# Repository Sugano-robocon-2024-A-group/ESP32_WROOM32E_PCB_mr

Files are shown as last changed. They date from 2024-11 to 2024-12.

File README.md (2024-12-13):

# ESP32_WROOM_32E_msd
## 作成・許諾 
Copyright (c) [2024] [益田隆太郎]. All rights reserved.
Sugano Robocon Aチーム (益田隆太郎、大谷卓輝、須崎一眞、藤上晃成)  
### * このソフトウェアパッケージは、3条項BSDライセンスの下、再配布及び使用が許可されます
### @ 2024 Sugano Robocon A team
連絡はX(@Masuda_moto)またはryutaro.masuda@akane.waseda.jpまで
## 外観
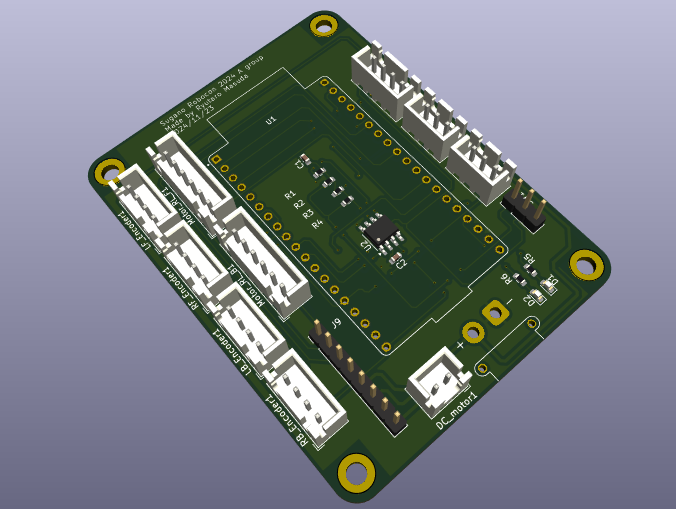
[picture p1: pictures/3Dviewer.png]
3Dviewr

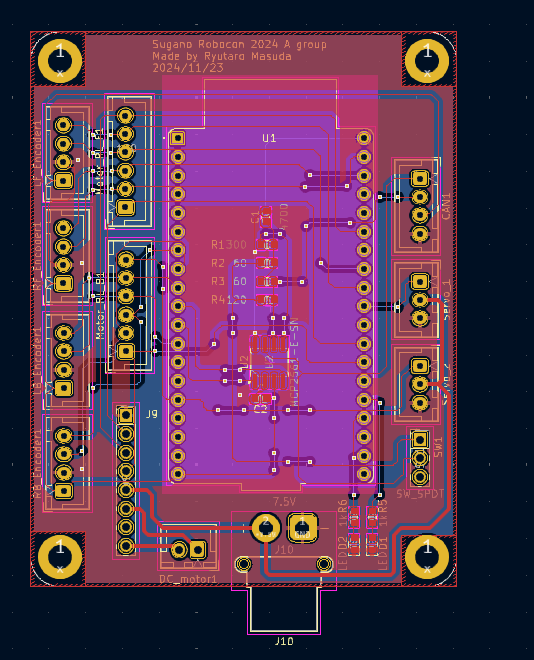
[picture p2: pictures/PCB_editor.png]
PCBViwer

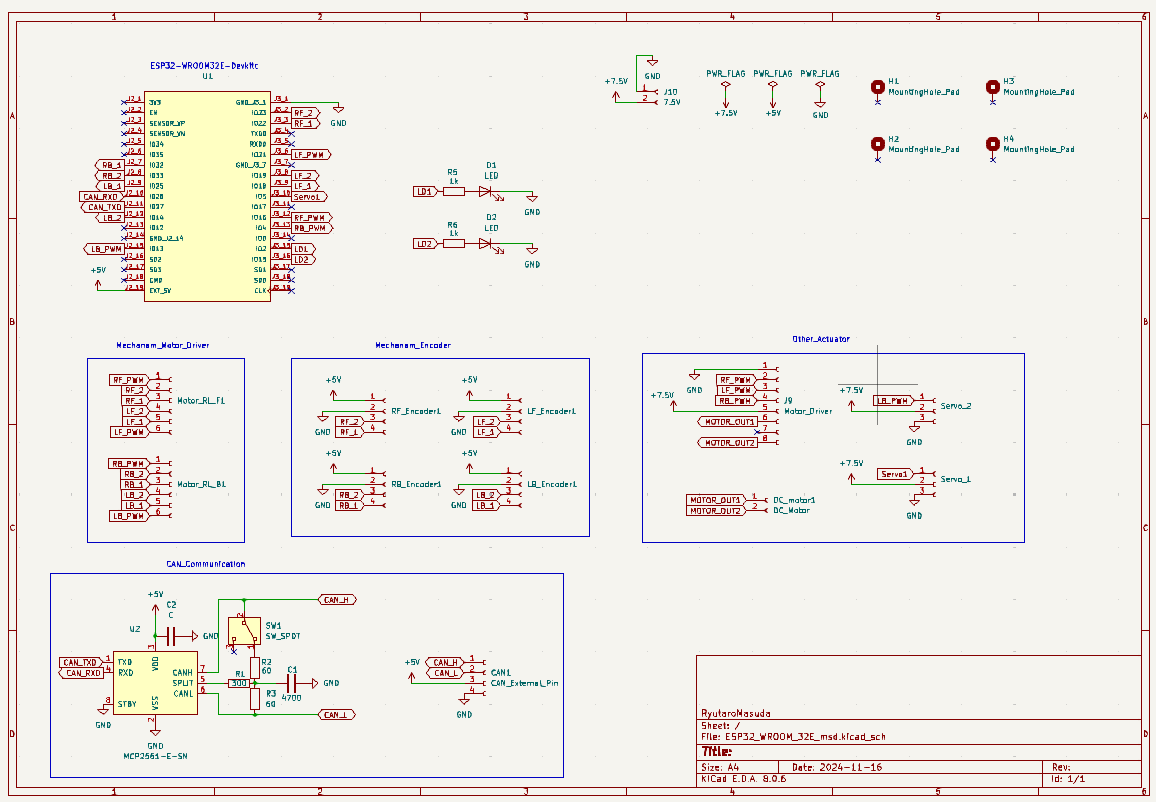
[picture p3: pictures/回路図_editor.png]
回路図

## 使用法
production→ESP32_WROOM_32E_msd.zipがガーバーファイルで、JLCPCBに送るとそのままPCBとして出してくれます。
## ピン配置
ESP32はESPマトリックス機能があるため、どのピンを使っても基本的に許されるが、PWMがはけるピンは決まっている。
[こちら](https://docs.sunfounder.com/projects/umsk/ja/latest/07_appendix/esp32_wroom_32e.html)を参照のこと
を参照のこと。
### 足回りピン配置
回路図の通りですが
RFはRightFront、LFはLeftFront、RBはRightBack、LBはLeftBackに対応しています。(例:RF_1とRF_2でモータドライバの正転逆転を制御、RF_PWMで角速度を制御)

GPIO22 RF_1  
GPIO23 RF_2  
GPIO16 RF_PWM  
GPIO18 LF_1  
GPIO19 LF_2  
GPIO21 LF_PWM  
GPIO32 RB_1  
GPIO33 RB_2  
GPIO04 RB_PWM  
GPIO25 LB_1  
GPIO14 LB_2  
GPIO13 LB_PWM  
足回りのモータドライバは[こちら](https://osoyoo.com/2022/02/25/osoyoo-model-y-4-channel-motor-driver/)の市販品を使用しました。

### CAN通信
いろんなサイトで26と27がRXとTXにアサインされていたので使用。うまく動きました。

GPIO26 CAN_RX  
GPIO27 CAN_TX  

### エンコーダピン配置
エンコーダで速度制御のフィードバックをかけたかったのですが、それだとピンが足りません。なのでマイコンを2個使って、CAN通信で情報をおくりあうことにしました。二つのマイコンの基板を共通化させたかったので、ピンを共有させました。
本番では速度のPID制御はあきらめてフィードフォワード制御に変えたので、このピンは使っていません。使いたかったら使うと良いと思います。
この場合、①RFとLFのモータを制御するマイコン②RBとLBのモータを制御するマイコン③上物を制御するマイコンの３つのマイコンでCAN通信をする必要があります。この時、CANバス内のノードが３つなので、終端抵抗を一つの基板だけOFFにする必要があります。SW1はそれ用のスイッチです。
また、ピンが共通になっているので、①のマイコンにおいて

GPIO22 RF_1  
GPIO23 RF_2  
GPIO16 RF_PWM  
GPIO18 LF_1  
GPIO19 LF_2  
GPIO21 LF_PWM  

をモータドライバに接続するときは、エンコーダに接続するピンは

GPIO32 RB_1  
GPIO33 RB_2  
GPIO25 LB_1  
GPIO14 LB_2  

であるという紛らわしさに注意する必要があります。②はその逆で、

GPIO32 RB_1  
GPIO33 RB_2  
GPIO04 RB_PWM  
GPIO25 LB_1  
GPIO14 LB_2  
GPIO13 LB_PWM  

をモータドライバに接続するので、エンコーダに接続するピンは

GPIO22 RF_1  
GPIO23 RF_2  
GPIO18 LF_1  
GPIO19 LF_2  

です。回路図の通りですね。
### 上物
投擲用のモータドライバは秋月で買える[TB67H450](https://akizukidenshi.com/catalog/g/g114753/)を使いました。
投擲のモータは速度フィードバックはかけず、フィードフォワードのみです。

GPIO16 RF_PWM 正転・逆転  
GPIO21 LF_PWM 正転・逆転  
GPIO04 RB_PWM PWM調整  

です。

GPIO13 LB_PWM  
GPIO05 Servo1  

を装填・仰角調整にアサインしました。
上物の電源電圧は2Sのリポバッテリー7.4Vを使用しました。XT30がコネクタです。

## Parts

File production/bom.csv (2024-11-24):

Designator | Footprint | Quantity | Value | LCSC Part #
C1 | 0603 | 1 | 4700
C2 | 0603 | 1 | C
CAN1 | JST_XH_B4B-XH-A_1x04_P2.50mm_Vertical | 1 | CAN_External_Pin
D1, D2 | 0603 | 2 | LED
DC_MOTOR1 | JST_XH_B2B-XH-A_1x02_P2.50mm_Vertical | 1 | DC_Motor
H1, H2, H3, H4 | MountingHole_3.2mm_M3_DIN965_Pad | 4 | MountingHole_Pad
J10 | AMASS_XT30PW-F_1x02_P2.50mm_Horizontal | 1 | 7.5V
J9 | PinHeader_1x08_P2.54mm_Vertical | 1 | Motor_Driver
LB_ENCODER1 | JST_XH_B4B-XH-A_1x04_P2.50mm_Vertical | 1 | LB_Encoder
LF_ENCODER1 | JST_XH_B4B-XH-A_1x04_P2.50mm_Vertical | 1 | LF_Encoder
MOTOR_RL_B1 | JST_XH_B6B-XH-A_1x06_P2.50mm_Vertical | 1 | Motor_RL_B
MOTOR_RL_F1 | JST_XH_B6B-XH-A_1x06_P2.50mm_Vertical | 1 | Motor_RL_F
R1 | 0603 | 1 | 300
R2, R3 | 0603 | 2 | 60
R4 | 0603 | 1 | 120
R5, R6 | 0603 | 2 | 1k
RB_ENCODER1 | JST_XH_B4B-XH-A_1x04_P2.50mm_Vertical | 1 | RB_Encoder
RF_ENCODER1 | JST_XH_B4B-XH-A_1x04_P2.50mm_Vertical | 1 | RF_Encoder
SERVO_1 | JST_XH_B3B-XH-A_1x03_P2.50mm_Vertical | 1 | Servo_1
SERVO_2 | JST_XH_B3B-XH-A_1x03_P2.50mm_Vertical | 1 | Servo_2
SW1 | PinHeader_1x03_P2.54mm_Vertical | 1 | SW_SPDT
U1 | MODULE_ESP32-DEVKITC-32E | 1 | ~
U2 | SOIC-8_3.9x4.9mm_P1.27mm | 1 | MCP2561-E-SN

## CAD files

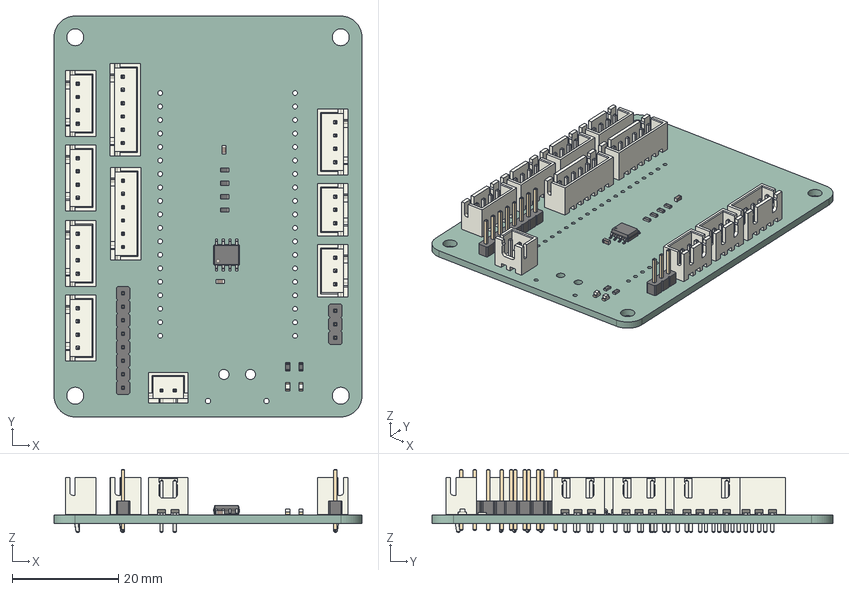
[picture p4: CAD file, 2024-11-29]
ESP32_WROOM_32E_msd.step
58.0 x 75.5 x 11.9 mm
JST_B4B_XH_A x 5
LED_0603_1608Metric x 2
C_0603_1608Metric x 2
PinHeader_1x08_P254mm_Vertical
R_0603_1608Metric x 6
SOIC_8_39x49mm_P127mm
JST_B6B_XH_A x 2
JST_B3B_XH_A x 2
JST_B2B_XH_A
PinHeader_1x03_P254mm_Vertical
_autosave-ESP32_WROOM_32E_msd_PCB

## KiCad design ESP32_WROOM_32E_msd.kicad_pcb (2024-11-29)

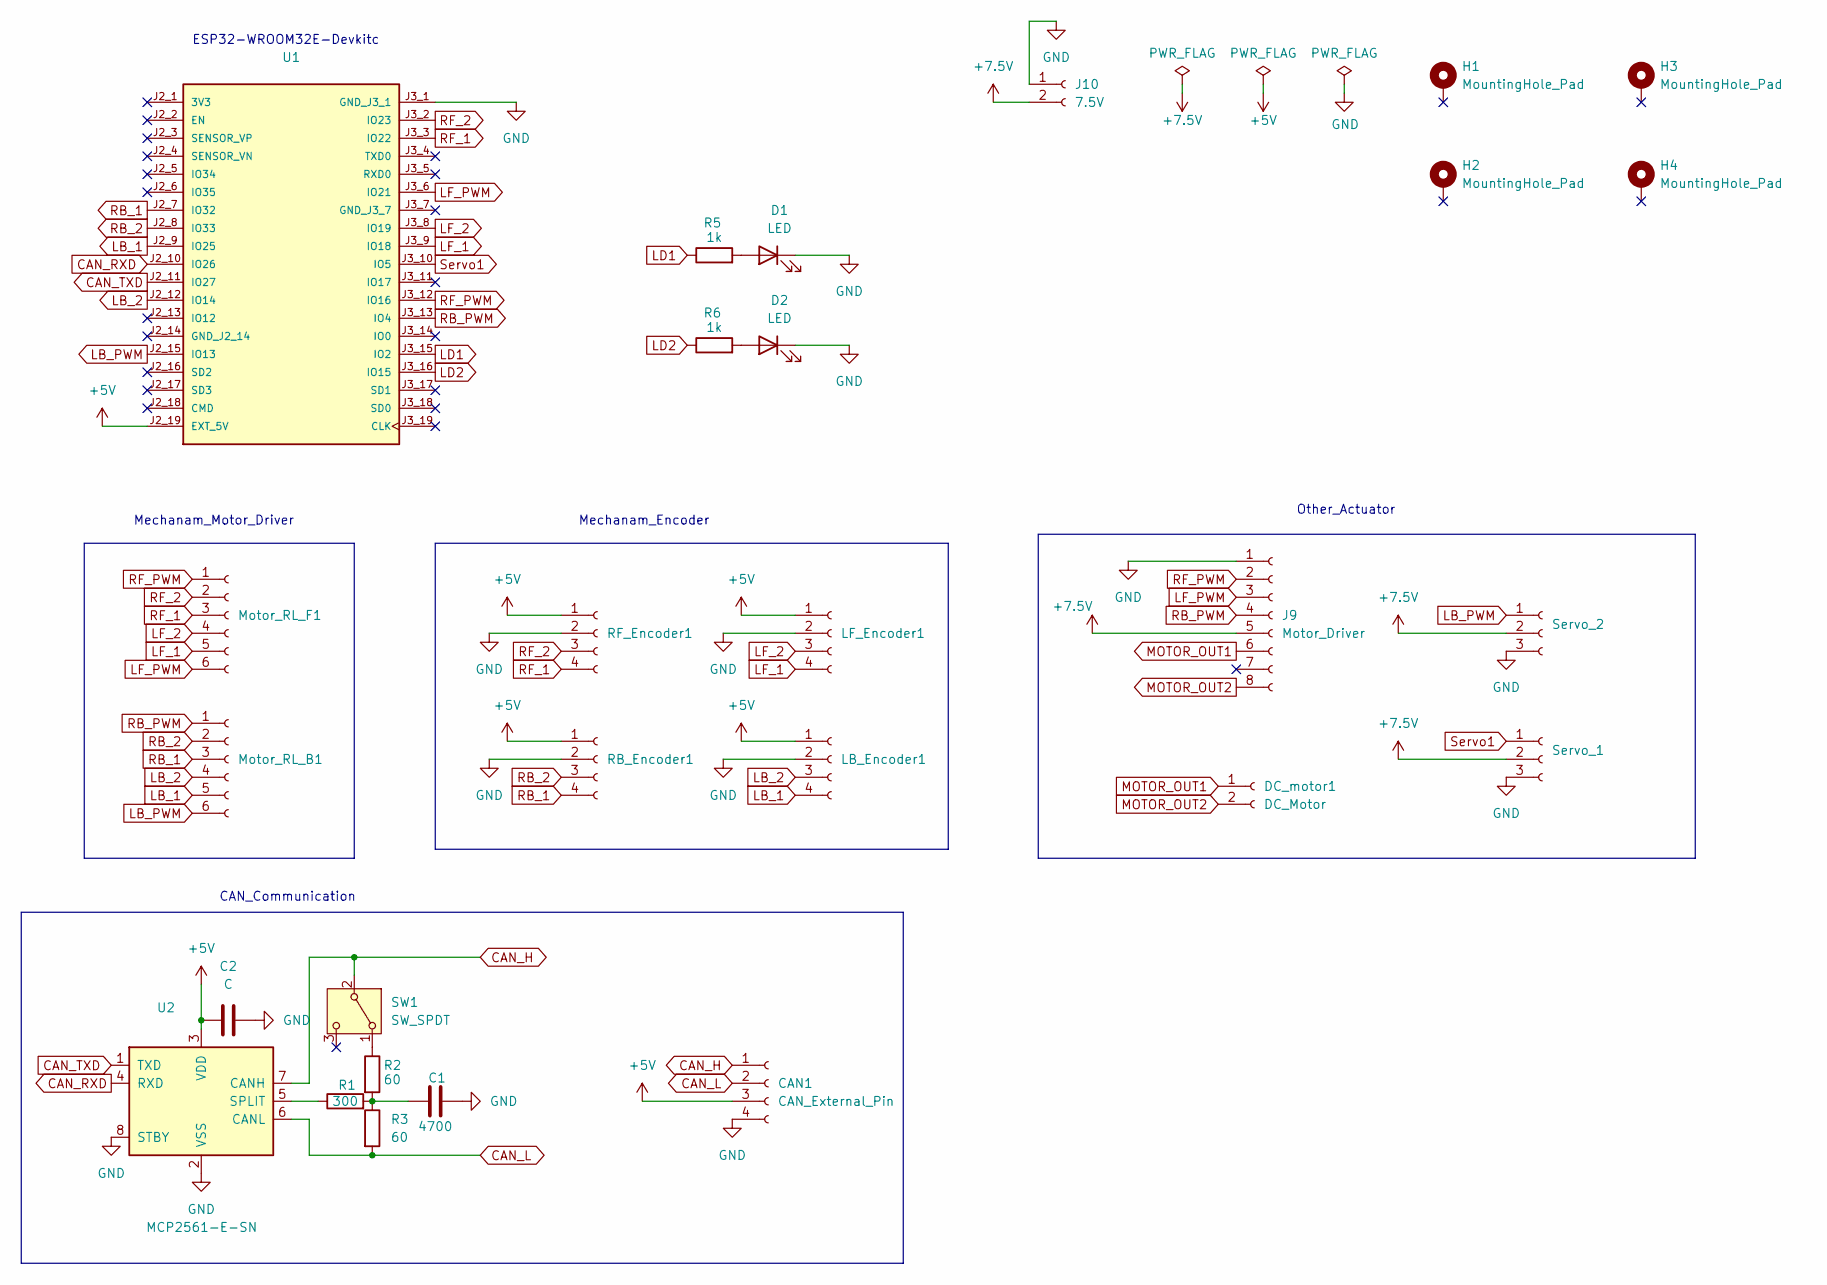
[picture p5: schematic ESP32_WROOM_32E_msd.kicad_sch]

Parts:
C1: 4700; C_0603_1608Metric
C2: C; C_0603_1608Metric
CAN1: CAN_External_Pin; JST_XH_B4B-XH-A_1x04_P2.50mm_Vertical
D1, D2: LED; LED_0603_1608Metric
DC_motor1: DC_Motor; JST_XH_B2B-XH-A_1x02_P2.50mm_Vertical
H1, H2, H3, H4: MountingHole_Pad; MountingHole_3.2mm_M3_DIN965_Pad
J9: Motor_Driver; PinHeader_1x08_P2.54mm_Vertical
J10: 7.5V; AMASS_XT30PW-F_1x02_P2.50mm_Horizontal
LB_Encoder1: LB_Encoder; JST_XH_B4B-XH-A_1x04_P2.50mm_Vertical
LF_Encoder1: LF_Encoder; JST_XH_B4B-XH-A_1x04_P2.50mm_Vertical
Motor_RL_B1: Motor_RL_B; JST_XH_B6B-XH-A_1x06_P2.50mm_Vertical
Motor_RL_F1: Motor_RL_F; JST_XH_B6B-XH-A_1x06_P2.50mm_Vertical
R1: 300; R_0603_1608Metric
R2, R3: 60; R_0603_1608Metric
R5, R6: 1k; R_0603_1608Metric
RB_Encoder1: RB_Encoder; JST_XH_B4B-XH-A_1x04_P2.50mm_Vertical
RF_Encoder1: RF_Encoder; JST_XH_B4B-XH-A_1x04_P2.50mm_Vertical
SW1: SW_SPDT; PinHeader_1x03_P2.54mm_Vertical
Servo_1: Servo_1; JST_XH_B3B-XH-A_1x03_P2.50mm_Vertical
Servo_2: Servo_2; JST_XH_B3B-XH-A_1x03_P2.50mm_Vertical
U1: MODULE_ESP32-DEVKITC-32E; PARTREV 1.4
U2: MCP2561-E-SN; SOIC-8_3.9x4.9mm_P1.27mm

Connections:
+5V: C2.1, CAN1.3, LB_Encoder1.1, LF_Encoder1.1, RB_Encoder1.1, RF_Encoder1.1, U1.J2_19 (EXT_5V), U2.3 (VDD)
+7.5V: J9.5, J10.2, Servo_1.2, Servo_2.2
CAN_H: CAN1.1, SW1.2 (B), U2.7 (CANH)
CAN_L: CAN1.2, R3.2, U2.6 (CANL); also elsewhere on the board
CAN_RXD: U1.J2_10 (IO26), U2.4 (RXD)
CAN_TXD: U1.J2_11 (IO27), U2.1 (TXD)
GND: C1.2, C2.2, CAN1.4, D1.1 (K), D2.1 (K), J9.1, J10.1, LB_Encoder1.2, LF_Encoder1.2, RB_Encoder1.2, RF_Encoder1.2, Servo_1.3, Servo_2.3, U1.J3_1 (GND_J3_1), U2.2 (VSS), U2.8 (STBY)
LB_1: LB_Encoder1.4, Motor_RL_B1.5, U1.J2_9 (IO25)
LB_2: LB_Encoder1.3, Motor_RL_B1.4, U1.J2_12 (IO14)
LB_PWM: Motor_RL_B1.6, Servo_2.1, U1.J2_15 (IO13)
LD1: R5.1, U1.J3_15 (IO2)
LD2: R6.1, U1.J3_16 (IO15)
LF_1: LF_Encoder1.4, Motor_RL_F1.5, U1.J3_9 (IO18)
LF_2: LF_Encoder1.3, Motor_RL_F1.4, U1.J3_8 (IO19)
LF_PWM: J9.3, Motor_RL_F1.6, U1.J3_6 (IO21)
MOTOR_OUT1: DC_motor1.1, J9.6
MOTOR_OUT2: DC_motor1.2, J9.8
unnamed: C1.1, R1.2, R2.2, R3.1
unnamed: D1.2 (A), R5.2
unnamed: D2.2 (A), R6.2
unnamed 20: R2.1, SW1.1 (A); also elsewhere on the board
unnamed: R1.1, U2.5 (SPLIT)
RB_1: Motor_RL_B1.3, RB_Encoder1.4, U1.J2_7 (IO32)
RB_2: Motor_RL_B1.2, RB_Encoder1.3, U1.J2_8 (IO33)
RB_PWM: J9.4, Motor_RL_B1.1, U1.J3_13 (IO4)
RF_1: Motor_RL_F1.3, RF_Encoder1.4, U1.J3_3 (IO22)
RF_2: Motor_RL_F1.2, RF_Encoder1.3, U1.J3_2 (IO23)
RF_PWM: J9.2, Motor_RL_F1.1, U1.J3_12 (IO16)
Servo1: Servo_1.1, U1.J3_10 (IO5)

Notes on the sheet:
Mechanam_Motor_Driver
Other_Actuator
ESP32-WROOM32E-Devkitc
CAN_Communication
Mechanam_Encoder

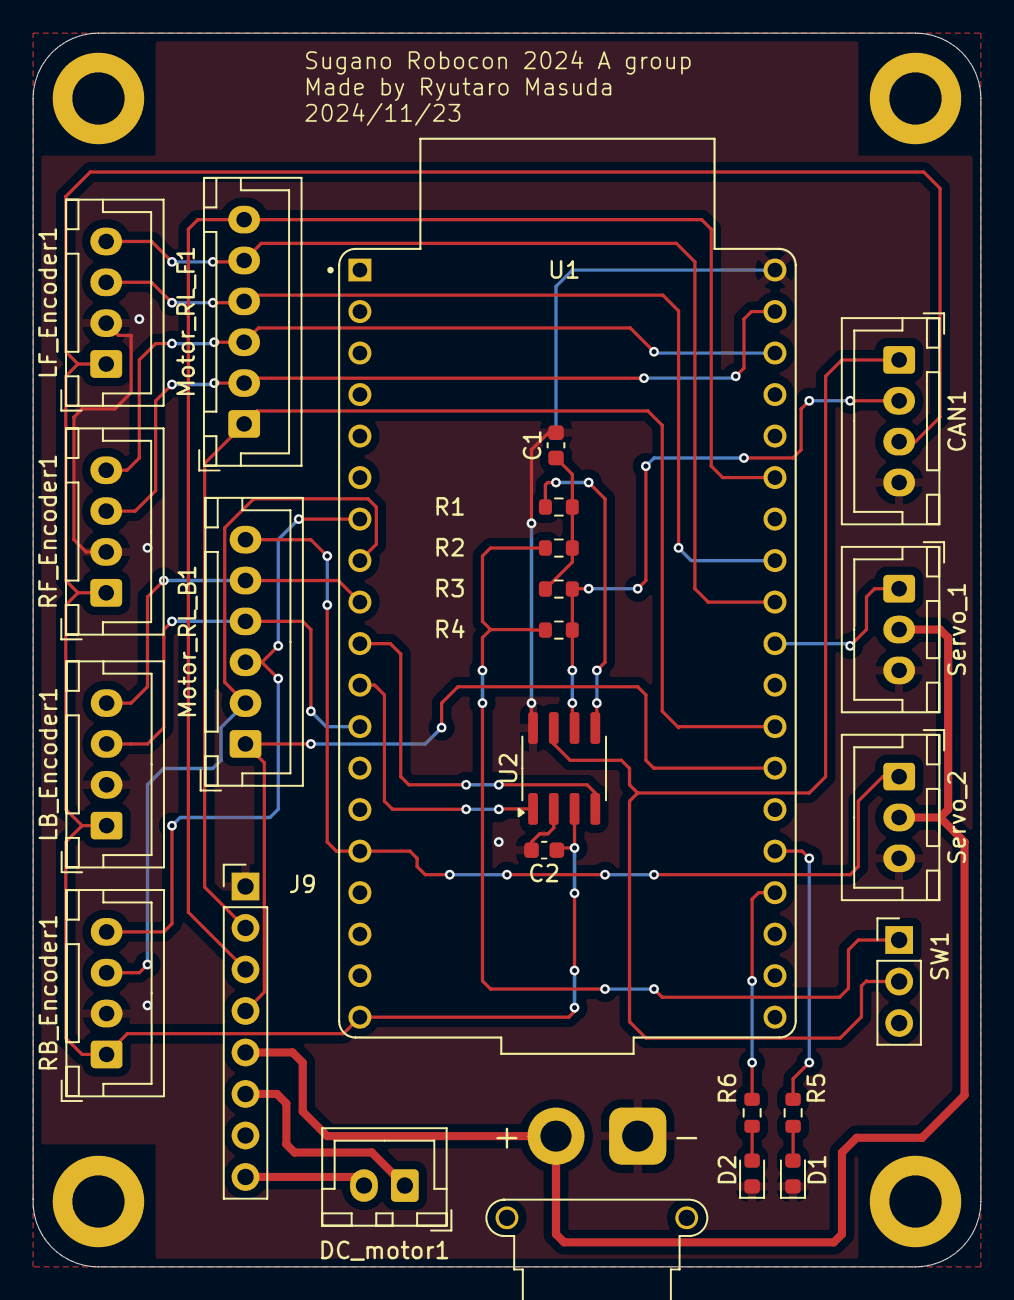
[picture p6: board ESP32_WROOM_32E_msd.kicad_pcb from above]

Board: 2 copper layers, 58.0 x 75.5 mm, 29 parts (0 on the bottom side), 29 nets.

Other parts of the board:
R4: 120; R_0603_1608Metric

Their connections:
CAN_L: R4.2; also elsewhere on the board
unnamed 20: R4.1; also elsewhere on the board

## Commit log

2024-11-15 second commit
    [ESP32_WROOM_32E_msd.kicad_pcb, ESP32_WROOM_32E_msd.kicad_sch]
2024-11-15 complete pcb
    [ESP32_WROOM_32E_msd.kicad_pcb, ESP32_WROOM_32E_msd.kicad_sch]
2024-11-19 add mickey
    [ESP32_WROOM_32E_msd.kicad_pcb, bom.csv, designators.csv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]
2024-11-22 add encoder pin and motor driver pin
    XH_4×4, pin header_8×1
    [ESP32_WROOM_32E_msd.kicad_pcb, ESP32_WROOM_32E_msd.kicad_sch]
2024-11-22 add frames
    [ESP32_WROOM_32E_msd.kicad_sch]
2024-11-24 almost complete
    add Beta Ground,
    [ESP32_WROOM_32E_msd.kicad_pcb, ESP32_WROOM_32E_msd.kicad_sch]
2024-11-24 complete ver2
    [ESP32_WROOM_32E_msd.kicad_pcb, bom.csv, designators.csv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]
2024-11-24 change switch
    because no stock on JLCPCB
    [ESP32_WROOM_32E_msd.kicad_pcb, ESP32_WROOM_32E_msd.kicad_sch]
2024-11-24 revised wiring thickness
    アクチュエータ部の配線太さを変更
    [ESP32_WROOM_32E_msd.kicad_pcb, ESP32_WROOM_32E_msd.kicad_sch, bom.csv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]
2024-11-29 add step file
    [ESP32_WROOM_32E_msd.step]
2024-12-13 add pictures
    [ESP32_WROOM_32E_msd.kicad_pcb]
